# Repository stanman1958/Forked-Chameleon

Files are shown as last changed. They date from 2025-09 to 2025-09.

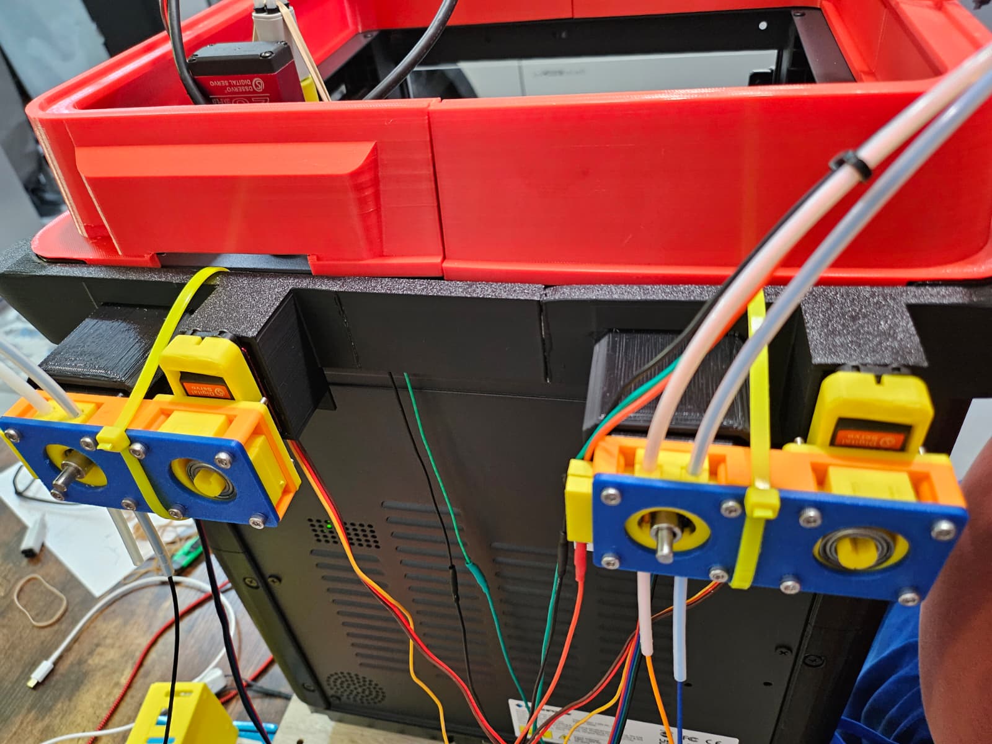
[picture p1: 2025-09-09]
Pictures/Rear View.jpg

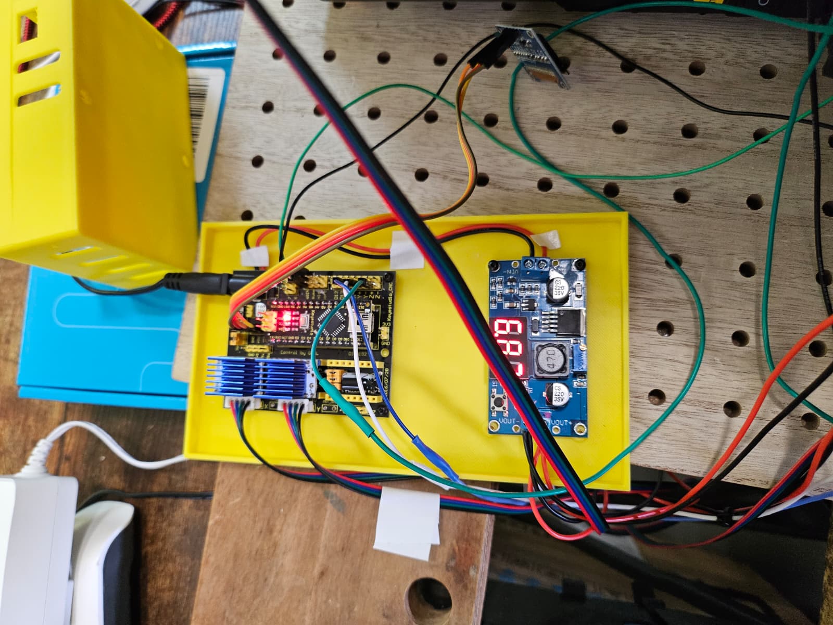
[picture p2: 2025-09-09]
Pictures/Controller.JPG

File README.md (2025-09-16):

# Forked-Chameleon
This is the collection of parts, BOMs, code, etc for my fork of the 3DChameleon, specifically for the FlashForge AD5M.

You are free to copy, modify, etc with attribution.

I started this after trying to get the original 3DChameleon to work.  I am sure that it would have worked, with a lot of tuning and adjustments to 
compensate for any tolerance issues.  I decided to take a different approach and the result was what I am calling the Forked Chameleon.

My issues were primarily around the selector portion of the 3DChameleon.  I could not consistently/repeatedly select a specific filament, at times have two filaments active.  
By splitting the 3DChameleon into two separate pieces, each one only selecting between 1 of 2 possible filaments and that selection excluding the other filament I was able to 
achieve repeatable and predictable fialment selection.

The original 3DChameleon used two stepper motors, one as an extruder the fed the filaments to the toolhead with the other stepper basically function as a servo, rotating a cam
with two bearings, driving the two halves of the 3DChameleon and forcing a filament against the extruder gear.  My fork uses two steppers but each is part of a separate assembly,
a Chameleon.  In place of the stepper used to rotate the cam, I use a servo that rotates a modifies cam with a single bearing that then selects 1 of the 2 filaments.  So, at the expense of adding two servos I was able to simplify the mechanics of selecting and feeding the filaments.

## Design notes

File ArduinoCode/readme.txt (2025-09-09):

This folder contatins the latest Arduino Code for the Forked Chameleon...

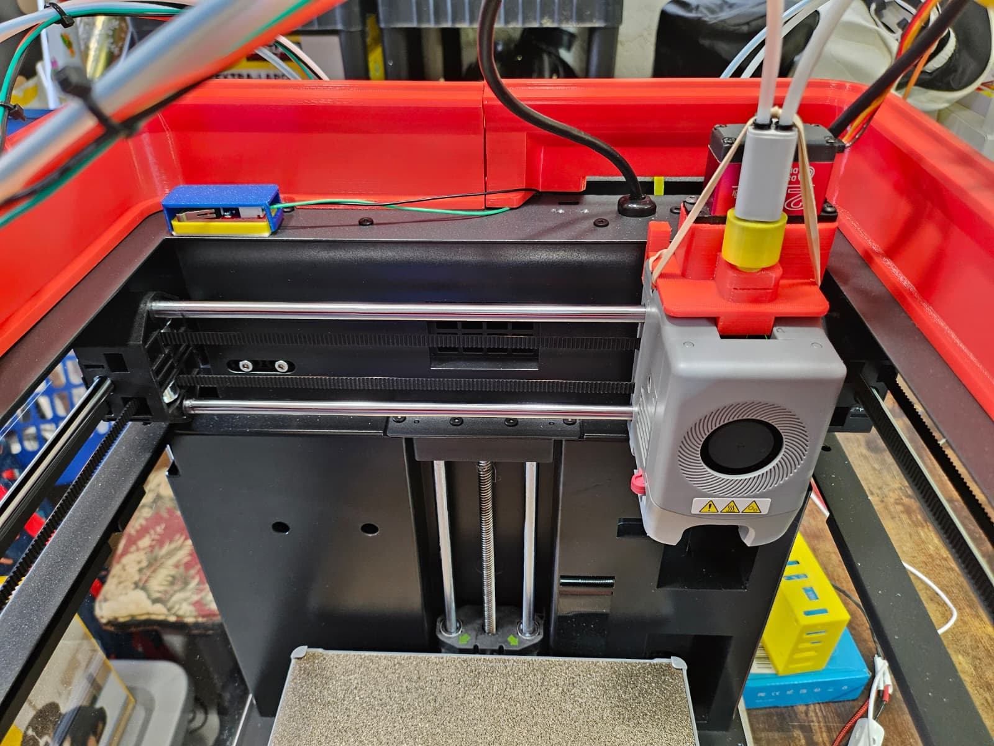
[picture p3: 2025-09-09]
Pictures/Front View.jpg

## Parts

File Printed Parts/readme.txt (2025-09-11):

These are the current printed parts I am using in my Forked Chameleon

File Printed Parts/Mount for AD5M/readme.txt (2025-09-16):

These are the 3 printed parts for mounted the Forked Chameleon (Chameleons A & B) on the back of the 
FlashForge AD5M that has the enclosure printed parts installed.

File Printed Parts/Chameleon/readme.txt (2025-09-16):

These are the parts for 1 of the filament selector assemblies.

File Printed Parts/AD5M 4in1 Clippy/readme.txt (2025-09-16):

These are the 3 printed parts needed for my version of the 3DClippy, using the Bambu A1 Mini 4in1

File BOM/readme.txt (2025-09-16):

Placeholder for the various BOMs to be uploaded

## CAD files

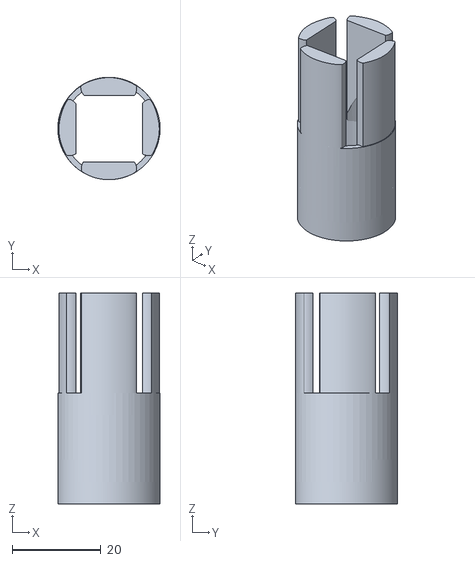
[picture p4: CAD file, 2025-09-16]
Printed Parts/AD5M 4in1 Clippy/AD5M Clippy for 4in1 Adapter Sleeve.stl
23.0 x 23.0 x 47.5

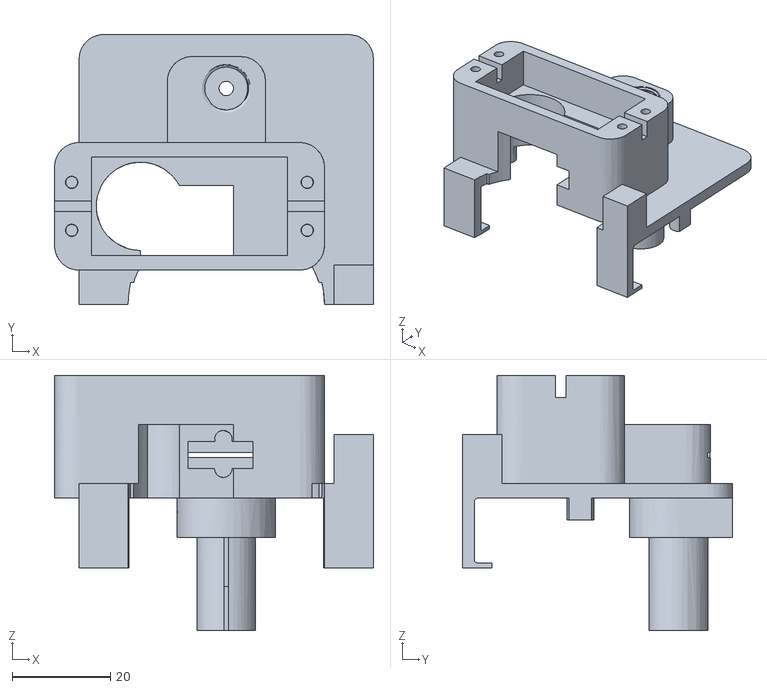
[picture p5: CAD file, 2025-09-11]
Printed Parts/Forked Chameleon AD5M Auto Clippy.stl
65.0 x 55.0 x 52.0

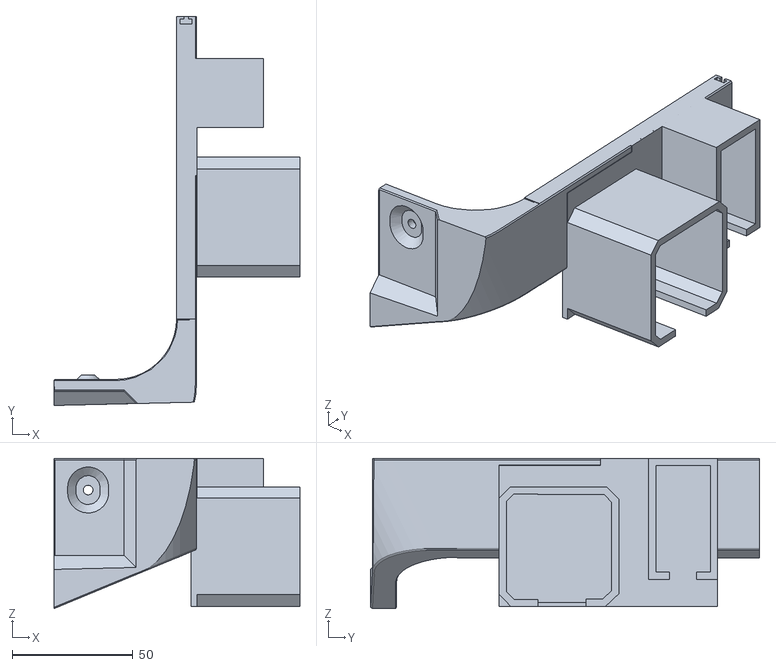
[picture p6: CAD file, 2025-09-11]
Printed Parts/Mount for AD5M/Forked Chameleon AD5M Right Rear Mount.stl
101.6 x 160.8 x 62.1

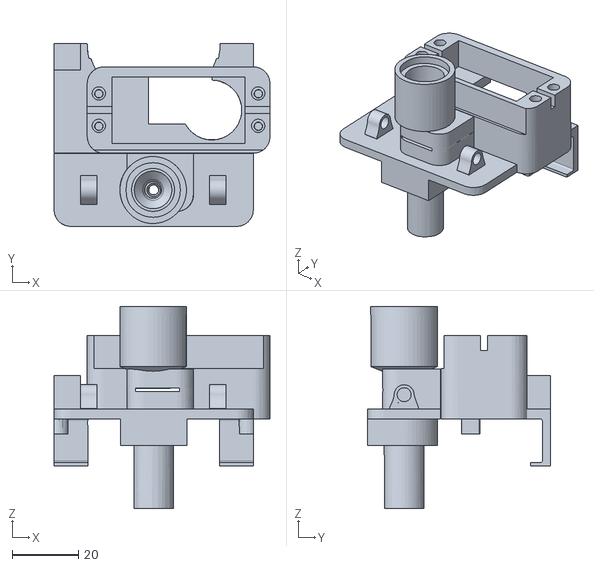
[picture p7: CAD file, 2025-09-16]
Printed Parts/AD5M 4in1 Clippy/AD5M Clippy for 4in1.stl
65.0 x 55.0 x 60.8

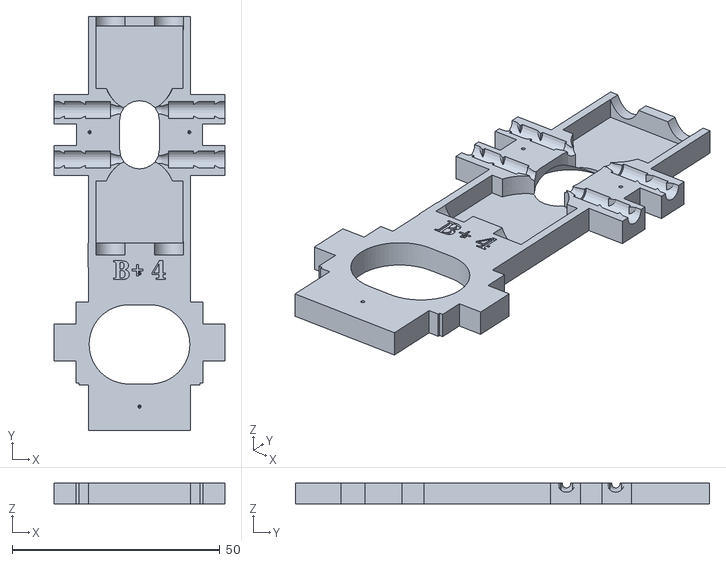
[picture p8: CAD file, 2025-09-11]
Printed Parts/Chameleon/Forked Chameleon C Part.stl
41.0 x 99.5 x 5.00

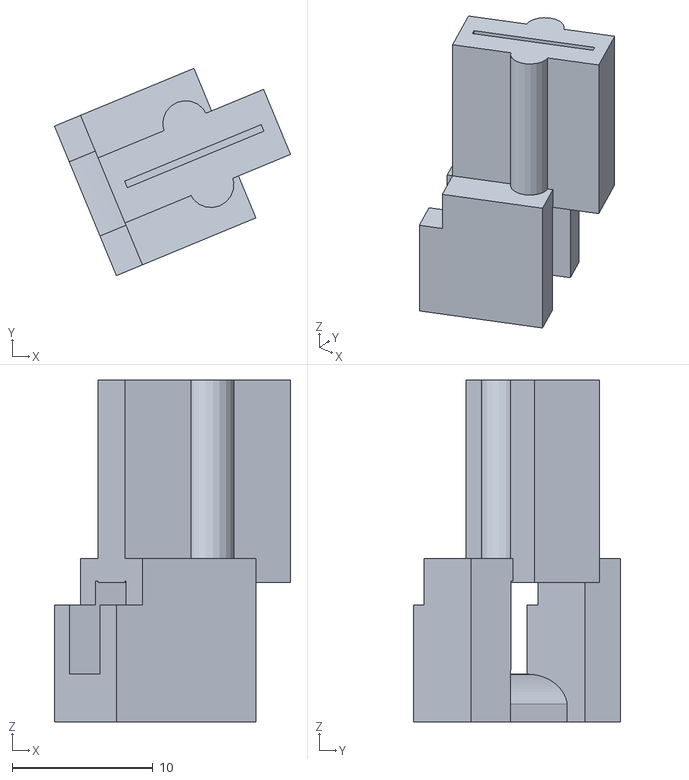
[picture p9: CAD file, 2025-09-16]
Printed Parts/AD5M 4in1 Clippy/FF_AD5M 3d Chameleon Auto Clippy Blade.stl
16.8 x 14.7 x 24.3

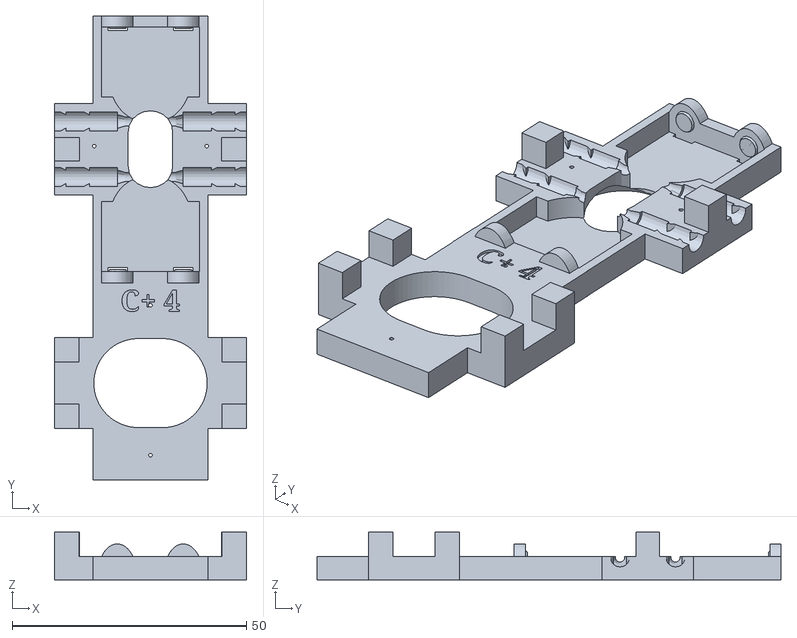
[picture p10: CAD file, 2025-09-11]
Printed Parts/Chameleon/Forked Chameleon B Part.stl
41.0 x 99.1 x 10.3

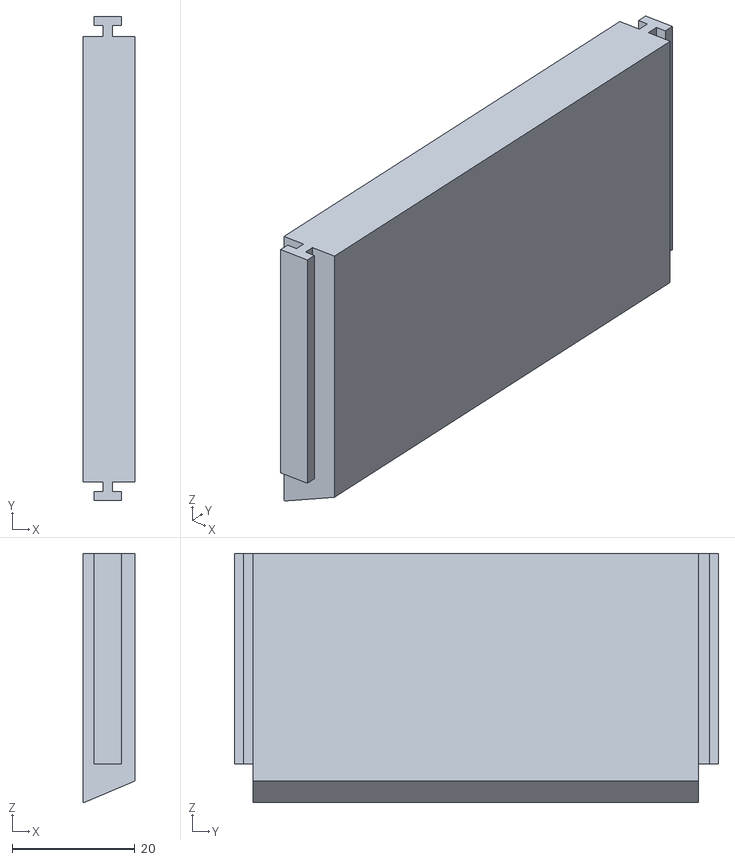
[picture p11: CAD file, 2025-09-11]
Printed Parts/Mount for AD5M/Forked Chameleon AD5M Mount Spacer.stl
8.50 x 78.8 x 40.5

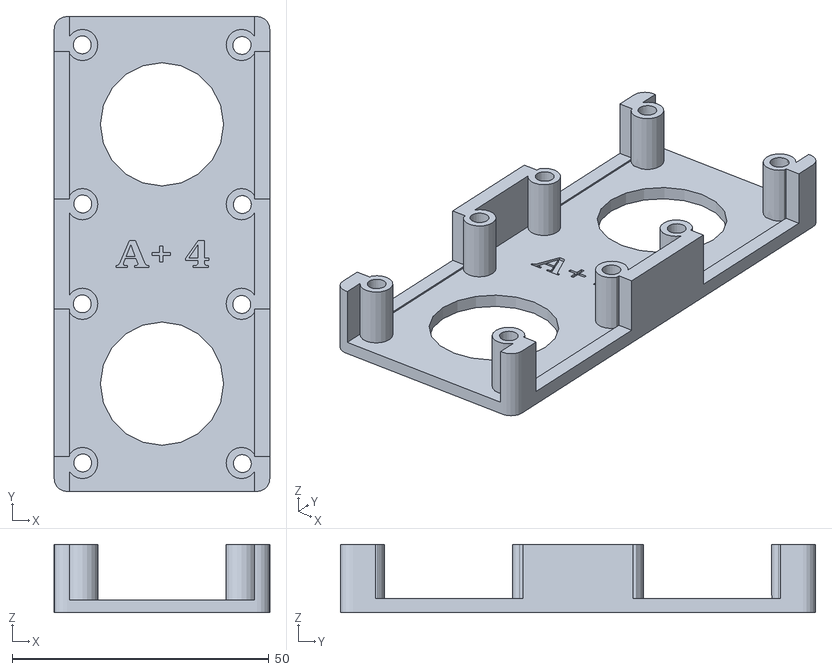
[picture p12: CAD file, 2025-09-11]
Printed Parts/Chameleon/Forked Chameleon Base.stl
42.0 x 92.5 x 13.2

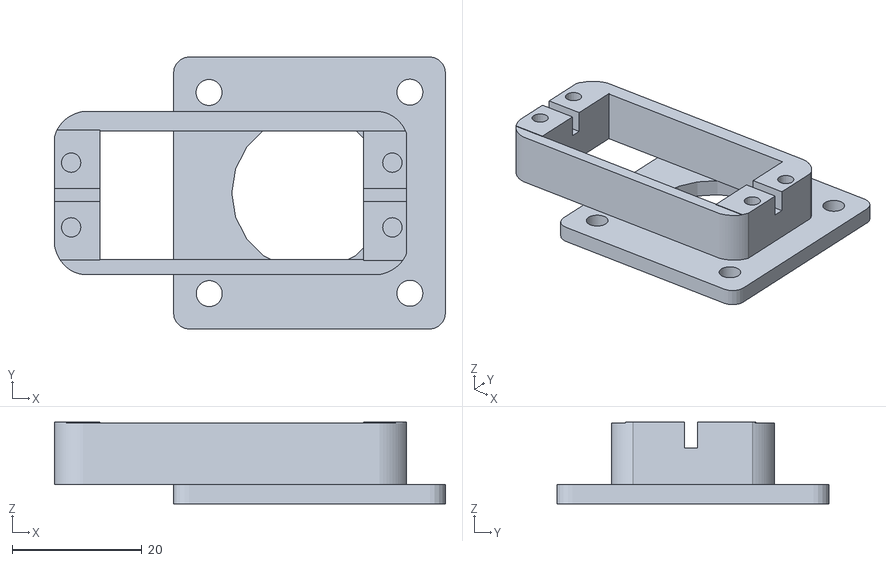
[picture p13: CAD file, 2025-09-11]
Printed Parts/Chameleon/Forked Chameleon Servo Mount.stl
60.4 x 42.0 x 12.6

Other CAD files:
Printed Parts/Chameleon/Forked Chameleon Servo Cam.stl
Printed Parts/Mount for AD5M/Forked Chameleon AD5M Left Rear Mount.stl

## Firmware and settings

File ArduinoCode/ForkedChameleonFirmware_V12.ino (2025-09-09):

// August 11, 2025

/* Forked Chameleon Firmware

Copyright 2025 Stan Peterson
Derived from 3D Chameleon MK4.1 Firmware & Hardware

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
Single Button Press Commands (count pulses of selector)

#1 - 1
#2 - 2
#3 - 3
#4 - 4
#5 - Cut and unload current filament
#9 - Cut filament, mainly for troubleshooting and failed prints
 
*/

#include <SSD1306Ascii.h> //i2C OLED
#include <SSD1306AsciiWire.h> //i2C OLED
#include <Wire.h>
#include <SPI.h>
#include <Servo.h>




#define SCREEN_WIDTH 128 // OLED display width, in pixels
#define SCREEN_HEIGHT 64 // OLED display height, in pixels


// Declaration for an SSD1306 display connected to I2C (SDA, SCL pins)
#define OLED_RESET  -1 // Reset pin # (or -1 if sharing Arduino reset pin)
#define OLED_I2C_ADDRESS 0x3C
SSD1306AsciiWire oled;

// Updates for CNC Sheild V4, X Motor Driver
#define extEnable 8

#define AChameleonStep 2
#define AChameleonDir 5

// Y Motor Drive
#define BChameleonStep 3
#define BChameleonDir 6


//#define RESET 13


#define trigger A3
//#define s_limit A4
//#define filament A5

const int stepsPerRev = 200;
const int microSteps = 16;
const int speedDelay = 240;

Servo filamentCutter;  // create servo object to control a servo
bool reverseServo = true;

Servo Selector1;
Servo Selector2;

Servo AChameleon;
Servo BChameleon;

int SelectorHome = 90;
int SelectorMin = 15;
int SelectorMax = 165;
int AChameleonOffset = -10;
int BChameleonOffset = 10;
int pos = 0;

int currentFilament = -1;
int lastFilament = -1;

long pulseTime = 200;


//int address = 0;
//byte value;

//long idleCount = 0;
//bool logoActive = false;
//bool T0Loaded = false;
//bool T1Loaded = false;
//bool T2Loaded = false;
//ool T3Loaded = false;

int load = 1;
int unload = 0;



//bool displayEnabled = false;
//bool ioEnabled = false;
//int sensorEnabled = 0;

//long randomNumber = 0;

void setup()
{

  Wire.begin(); //start i2C  
	Wire.setClock(400000L); //set clock

  // enable OLED display
  oled.begin(&Adafruit128x64, OLED_I2C_ADDRESS);

  // wait for it to start up
  delay(50);
    

  // welcome screen
  oled.setFont(Adafruit5x7);
  oled.clear(); //clear display
	oled.println("");
  oled.println("Welcome!"); //print a welcome message  
  oled.println("");
  oled.println("Forked Chameleon"); //print a welcome message
  oled.println("Version 12 Sep 6 2025");
  oled.println("Stan Peterson");
  delay(5000);

  Serial.begin(9600);

  


  // Sets the pins as Outputs
  pinMode(extEnable, OUTPUT);
  pinMode(AChameleonStep, OUTPUT);
  pinMode(AChameleonDir, OUTPUT);

  pinMode(BChameleonStep, OUTPUT);
  pinMode(BChameleonDir, OUTPUT);

 // pinMode(RESET, OUTPUT);
 // digitalWrite(RESET, HIGH);

  // set up the button
  pinMode(trigger, INPUT_PULLUP);  // selector button


// comment out the selector cycling code

// Cycle and Home the Selectors - streamline this after debugging
    Selector1.attach(9);
//Selector1.write(SelectorHome);
    for (pos = SelectorHome+AChameleonOffset; pos <= (SelectorMax+AChameleonOffset); pos += 5) { // goes from 0 degrees to 180 degrees
    // in steps of 1 degree
    Selector1.write(pos);              // tell servo to go to position in variable 'pos'
    delay(25);                       // waits 15ms for the servo to reach the position
  }
    delay(1000);
    for (pos = (SelectorMax+AChameleonOffset); pos >= (SelectorMin+AChameleonOffset); pos -= 5) { // goes from 180 degrees to 0 degrees
    Selector1.write(pos);              // tell servo to go to position in variable 'pos'
    delay(25);                       // waits 15ms for the servo to reach the position
    }
    delay(1000);
    for (pos = (SelectorMin+AChameleonOffset); pos <= SelectorHome+AChameleonOffset; pos += 5) { // goes from 0 degrees to 180 degrees
    // in steps of 1 degree
    Selector1.write(pos);              // tell servo to go to position in variable 'pos'
    delay(25);  
  }
    delay(1000);
    Selector1.detach();

  Selector2.attach(10);
//  Selector2.write(SelectorHome);
    for (pos = SelectorHome+BChameleonOffset; pos <= SelectorMax+BChameleonOffset; pos += 5) { // goes from 0 degrees to 180 degrees
    // in steps of 1 degree
    Selector2.write(pos);              // tell servo to go to position in variable 'pos'
    delay(25);                       // waits 15ms for the servo to reach the position
  }
    delay(1000);
    for (pos = SelectorMax+BChameleonOffset; pos >= SelectorMin+BChameleonOffset; pos -= 5) { // goes from 180 degrees to 0 degrees
    Selector2.write(pos);              // tell servo to go to position in variable 'pos'
    delay(25);                       // waits 15ms for the servo to reach the position
    }
    delay(1000);
    for (pos = SelectorMin+BChameleonOffset; pos <= SelectorHome+BChameleonOffset; pos += 5) { // goes from 0 degrees to 180 degrees
    // in steps of 1 degree
    Selector2.write(pos);              // tell servo to go to position in variable 'pos'
    delay(25);  
  }
  delay(1000);
  Selector2.detach();
  cutFilament(); // Cut any filament left in the toolhead, on start up, gives the user a chance to reposition the filament at the loading point
}

void loop()
{
  unsigned long nextPulse;
  unsigned long pulseCount = 0;
  // process button press
  if (digitalRead(trigger) != 0)
  {

    displayText(30, "Waiting for Trigger");}

    // keep counting until button is released
    while (digitalRead(trigger) == 0)
    {
      if(pulseCount<pulseTime)
      {
        pulseCount++;
        displayCommand(pulseCount);
      }
      delay(1000);  // each pulse is 1000 milliseconds apart 
    }
    processCommand(pulseCount); // ok... execute whatever command was caught (by pulse count)
    pulseCount = 0;
  // each loop adds 50ms delay, so that gets added AFTER the command is processed before the next one can start
  delay(50);
}

// display command for each button pulse
void displayCommand(long commandCount)
{
  switch(commandCount)
  {
  case 1:
    displayText(5, "Load Filament 1");
    break;
  case 2:
    displayText(5, "Load Filament 2");
    break;
  case 3:
    displayText(5, "Load Filament 3");
    break;
  case 4:
    displayText(5, "Load Filament 4");
    break;
  case 5:
    displayText(5, "Cut & Unload Current Filament");
    break;
  case 9:
    displayText(5, "Cut Filament");
    break;
  default:
    displayText(30, "     No Command");
    break;
  }
}

// execute the pulse count command
void processCommand(long commandCount)
{
  // select case for commands
  switch (commandCount)
  {
  case 1: // unload last loaded Filament (if there is one), load requested filament
    currentFilament = 1;
    displayText(5, "Filament 1 Selected");
    unloadFilament(lastFilament);
    loadFilament(currentFilament);
    displayText(5, "Filament 1 Ready");
    lastFilament = currentFilament;  //update the lastFilament to it's new value of the currentFilament
    break;

  case 2: // unload current, switch to #1, load
    displayText(5, "Filament 2 Selected");
    currentFilament = 2;
    unloadFilament(lastFilament);
    loadFilament(currentFilament);
    displayText(5, "Filament 2 Ready");
    lastFilament = currentFilament;  //update the lastFilament to it's new value of the currentFilament
    break;

  case 3: // unload current, switch to #3, load
    displayText(5, "Filament 3 Selected");
    currentFilament = 3;
    unloadFilament(lastFilament);
    loadFilament(currentFilament);
    displayText(5, "Filament 3 Ready");
    lastFilament = currentFilament;  //update the lastFilament to it's new value of the currentFilament
    break;

  case 4: // unload current, switch to #4, load
    displayText(5, "Filament 4 Selected");
    currentFilament = 4;
    unloadFilament(lastFilament);
    loadFilament(currentFilament);
    displayText(5, "Filament 4 Ready");
    lastFilament = currentFilament;  //update the lastFilament to it's new value of the currentFilament
    break;

  case 5: // unload current
    displayText(5, "Unload Filament " + String(lastFilament));
    unloadFilament(lastFilament);
    displayText(5, "Filament " + String(lastFilament) + " Unloaded");
    lastFilament = -1;
    currentFilament = -1;
    break;

//  case 11:                         //future add, reset the Forked Chameleon based on button trigger
//   digitalWrite(RESET, LOW);
//    delayMicroseconds(2);
//    digitalWrite(RESET,HIGH);
//    break;
  case 9:  // cut the filament, manual unload
      cutFilament();
      break;

  default:
    break;
  }
}

// just the routine to update the OLED
void displayText(int offset, String str)
{
    oled.clear();
    oled.println("");
    oled.println(str);
    oled.println("");
    Serial.println(str);
}



void loadFilament (int filament)
{
  switch(filament)
  {
    case 1:
      displayText(5, "Loading Filament 1");
      break;
    case 2:
      displayText(5, "Loading Filament 2");
      break;
    case 3:
      displayText(5, "Loading Filament 3");
      break;
    case 4:
      displayText(5, "Loading Filament 4");
      break;
  }
  selectFilament(filament);
  rotateExtruder(filament, load);
  releaseFilament();      
  // everybody remember where we parked!
lastFilament = currentFilament;
}

void unloadFilament (int filament)
{
  // make sure we have a real filament selected
  if(filament>0)
  {
    // if so, we need to cut the filament
//    displayText(30, "     Cutting...");
    cutFilament();

    // ok... then wait for the 2nd button press to unload it
    switch(filament)
    {
      case 1:
        displayText(5, "Unloading Filament 1");
        break;
      case 2:
        displayText(5, "Unloading Filament 2");
        break;
      case 3:
        displayText(5, "Unloading Filament 3");
        break;
      case 4:
        displayText(5, "Unloading Filament 4");
        break;
    } 

    selectFilament(filament);
    rotateExtruder(filament, unload);
    releaseFilament();    
  }
}



void selectFilament(int filament)
{
//      displayText(15,"Select Filament Sub " + String(filament));
//      delay(1000);
  int pos;
  int SelectorHome = 90;
  int SelectorMin = 0;
  int SelectorMax = 180;
  switch(filament){
    case 1:
      Selector1.attach(9);
      Selector1.write(SelectorMin+AChameleonOffset);              // tell servo to go to position in variable 'pos'
      delay(1000);                       // waits 1000ms for the servo to reach the position
      break;

    case 2:
      Selector1.attach(9);
      Selector1.write(SelectorMax+AChameleonOffset);              // tell servo to go to position in variable 'pos'
      delay(1000);                          // waits 1000ms for the servo to reach the position
      break;

    case 3:
      Selector2.attach(10);

      Selector2.write(SelectorMin+BChameleonOffset);              // tell servo to go to position in variable 'pos'
      delay(1000);                       // waits 15ms for the servo to reach the position
      break;

    case 4:
      Selector2.attach(10);
      Selector2.write(SelectorMax+BChameleonOffset);              // tell servo to go to position in variable 'pos'
      delay(1000);      // waits 15ms for the servo to reach the position
      break;
  }
}

void releaseFilament()
{
  //displayText(15,"Release Filament Sub");
//  delay(1000);
  Selector1.attach(9);
  Selector1.write(SelectorHome+AChameleonOffset);
    delay(1000);
  Selector1.detach();

  Selector2.attach(10);
  Selector2.write(SelectorHome+BChameleonOffset);
    delay(1000);
  Selector2.detach();
}

// move the extruder motor in a specific direction for a specific distance (unless it's a "until button is not pressed")
void rotateExtruder(int filament, int action)
{
      //displayText(15,"rotateExtruder Sub");
     // delay(500);
     int High = 1;
     int Low = 0;
    int direction;
    const int fastSpeed = speedDelay/2; // double time 
    const long loadTime = 3300; // 1800 did not load the tool head
    const long unloadTime = 1200; //
    int rotationTime;
    unsigned long startTime;

switch (action){
  case 1:
    rotationTime = loadTime;
    break;
  case 0:
    rotationTime = unloadTime;
    break;
}
// set direction depending upon filament and desired action (load or unload)
switch (filament){
  case 1:
    direction = !action;
    rotationTime = 1*rotationTime;
    break;
  case 2:
    direction = action;
    rotationTime = 1*rotationTime;
    break;
  case 3:
    direction = !action;
    rotationTime = 1.03*rotationTime; //the BChameleon seems to need a little extra seems to
    break;
  case 4:
    direction = action;
    rotationTime = 1.03*rotationTime;
  break;
}


//displayText(0,"Direction = " + String(direction));
//delay(1500);

switch (filament){
  case 1:
  case 2:
  digitalWrite(extEnable, LOW);  // lock the motor
  digitalWrite(AChameleonDir, direction); // Enables the motor to move in a particular direction

      startTime = millis();

      while (millis() - startTime < rotationTime)
    {

      // this is how we pulse the motor to get it to step
      digitalWrite(AChameleonStep, HIGH);
      delayMicroseconds(fastSpeed);
      digitalWrite(AChameleonStep, LOW);
      delayMicroseconds(fastSpeed);
    
    }
    break;

  case 3:
  case 4:
    digitalWrite(extEnable, LOW);  // lock the motor
    digitalWrite(BChameleonDir, direction); // Enables the motor to move in a particular direction
      startTime = millis();

      while (millis() - startTime < rotationTime)
    {

      // this is how we pulse the motor to get it to step
      digitalWrite(BChameleonStep, HIGH);
      delayMicroseconds(fastSpeed);
      digitalWrite(BChameleonStep, LOW);
      delayMicroseconds(fastSpeed);
    }
    break;
    }
  // ok
  digitalWrite(extEnable, HIGH);
}


// this cycles the Cutter servo between two positions
void cutFilament() {
//      displayText(15,"Inside Cut Filament Sub");
//      delay(500);
  filamentCutter.attach(11);

  if(reverseServo==false)
  {
    openGillotine();
    closeGillotine();
  }
  else
  {
    closeGillotine();
    openGillotine();
  }
  filamentCutter.detach();
}


// cycle servo from 135 and 180
void openGillotine()
{
    for (int pos = 135; pos <= 180; pos += 1) { // goes from 135 degrees to 180 degrees
    // in steps of 1 degree
    filamentCutter.write(pos);              // tell servo to go to position in variable 'pos'
    delayMicroseconds(25000);                       // waits 25ms for the servo to reach the position
  }
  delay(50);                       
}

// reverse cycle servo from 180 back to 135
void closeGillotine()
{
  for (int pos = 180; pos >= 135; pos -= 1) { // goes from 180 degrees to 135 degrees
    filamentCutter.write(pos);              // tell servo to go to position in variable 'pos'
    delayMicroseconds(25000);                       // waits 25ms for the servo to reach the position
  }
  delay(50);                       
}

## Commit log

2025-09-16 Rename Printed Parts/Forked Chameleon AD5M Auto Clippy.stl to Printed Parts/Old Parts/Forked Chameleon AD5M Auto Clippy.stl
    [Forked Chameleon AD5M Auto Clippy.stl]
2025-09-16 Rename Printed Parts/Forked Chameleon Top.stl to Printed Parts/Chameleon/Forked Chameleon Top.stl
    [Forked Chameleon Top.stl]
2025-09-16 Rename Printed Parts/Forked Chameleon B Part.stl to Printed Parts/Chameleon/Forked Chameleon B Part.stl
    [Forked Chameleon B Part.stl]
2025-09-16 Rename Printed Parts/Forked Chameleon Base.stl to Printed Parts/Chameleon/Forked Chameleon Base.stl
    [Forked Chameleon Base.stl]
2025-09-16 Rename Printed Parts/Forked Chameleon C Part.stl to Printed Parts/Chameleon/Forked Chameleon C Part.stl
    [Forked Chameleon C Part.stl]
2025-09-16 Rename Printed Parts/Forked Chameleon Servo Cam.stl to Printed Parts/Chameleon/Forked Chameleon Servo Cam.stl
    [Forked Chameleon Servo Cam.stl]
2025-09-16 Rename Printed Parts/Forked Chameleon Servo Mount.stl to Printed Parts/Chameleon/Forked Chameleon Servo Mount.stl
    [Forked Chameleon Servo Mount.stl]
2025-09-16 Rename Printed Parts/Forked Chameleon AD5M Left Rear Mount.stl to Printed Parts/Mount for AD5M/Forked Chameleon AD5M Left Rear Mount.stl
    [Forked Chameleon AD5M Left Rear Mount.stl]
2025-09-16 Rename Printed Parts/Forked Chameleon AD5M Mount Spacer.stl to Printed Parts/Mount for AD5M/Forked Chameleon AD5M Mount Spacer.stl
    [Forked Chameleon AD5M Mount Spacer.stl]
2025-09-16 Rename Printed Parts/Forked Chameleon AD5M Right Rear Mount.stl to Printed Parts/Mount for AD5M/Forked Chameleon AD5M Right Rear Mount.stl
    [Forked Chameleon AD5M Right Rear Mount.stl]
2025-09-16 Create AD5M 4in1 Clippy BOM
2025-09-16 Update and rename BOM.TXT to readme.txr
2025-09-16 Update AD5M 4in1 Clippy BOM
2025-09-16 Rename change_filament.gcode to Change Filament G-code
2025-09-16 Create Printing Notes
2025-09-17 Create Chameleon Bom
2025-09-17 Update Chameleon Bom
2025-09-17 Rename Chameleon Bom to Chameleon Sub-Assembly Bom
2025-09-17 Rename AD5M 4in1 Clippy BOM to AD5M 4in1 Clippy Sub-Assembly BOM
2025-09-17 Rename Forked Chameleon to Forked Chameleon Top Level Assembly
2025-11-10 Add Single Selector Firmware for filament control
    Initial commit of Single Selector Firmware for controlling filament loading and unloading.
